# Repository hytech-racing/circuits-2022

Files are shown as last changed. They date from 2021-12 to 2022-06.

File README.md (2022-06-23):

HyTech Logo

# 2022 Circuits

Repository for all of the circuits for the 2021-2022 car.

## Getting Started with this Git Repository
1. Create a GitHub account if you don't already have one.
2. Follow HyTech's [Software Guide](https://github.com/hytech-racing/training/tree/master/Resources).
3. Download and install [GitHub Desktop](https://desktop.github.com/) (basic) or [Git CLI](https://git-scm.com/book/en/v2/Getting-Started-Installing-Git) (advanced).
    * If you are using GitHub Desktop for the first time, be sure to read the [User Guide](https://help.github.com/desktop/guides/).
    * If you are using Git for the first time, you should start off by reading a tutorial. There are many available online:
        * [Git Tutorial](https://git-scm.com/docs/gittutorial)
        * [Atlassian Git Tutorial](https://www.atlassian.com/git/tutorials/)
    * You may want to keep a copy of [GitHub's Git Cheat Sheet](https://services.github.com/kit/downloads/github-git-cheat-sheet.pdf) as a reference.
4. Talk to your subteam lead to be added to the team within the GitHub organization.
5. Clone this repository to your computer using the URLs:
    * SSH: `git@github.com:hytech-racing/circuits-2022.git`
    * HTTPS: `https://github.com/hytech-racing/circuits-2022.git`

## Getting Started with EAGLE
1. Follow HyTech's [Software Guide](https://github.com/hytech-racing/training/tree/master/Resources).
2. Download and install Autodesk [EAGLE](https://www.autodesk.com/products/eagle/overview)
3. Get the free [Educational License](https://www.autodesk.com/education/free-software/eagle) (a .edu email address is required)

## Github Software Guidelines and Electrical Designs Rules Review Process
Follow HyTech's [Github Software Guidelines](https://gtvault.sharepoint.com/:w:/r/sites/HyTechRacing2/Shared%20Documents/Electrical%20-%20All/HT06/Guidelines%20Rules%20and%20Procedures/Github%20Software%20Guide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) to understand our development flow and pull request procedure.
Follow HyTech's [Electrical Designs Rules Review Process](https://gtvault.sharepoint.com/:w:/r/sites/HyTechRacing2/Shared%20Documents/Electrical%20-%20All/HT06/Guidelines%20Rules%20and%20Procedures/Electrical%20Designs%20Ru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) to understand circuit design flow. 

## Circuit Board Versioning Scheme
* New boards must start their numbering at revision 1.
* Revision numbers must be incremented by 1 when a physical board is manufactured, but not at any other time.
* After a board is manufactured, the files corresponding to the manufactured version should not be modified.
* Circuit boards based off of a previous year's design should increment based off of the previous board's revision number.

## More Information
* [Software Guide](https://github.com/hytech-racing/training/tree/master/Resources)
* [Team Site](https://hytechracing.gatech.edu/)
* [Facebook](https://www.facebook.com/HyTechRacing/)
* [Instagram](https://www.instagram.com/hytech.racing/)
* [Engage](https://gatech.campuslabs.com/engage/organization/hytech-racing)

## License
This project is licensed under the GPL License v3.0. See the [LICENSE](LICENSE) file for more information.

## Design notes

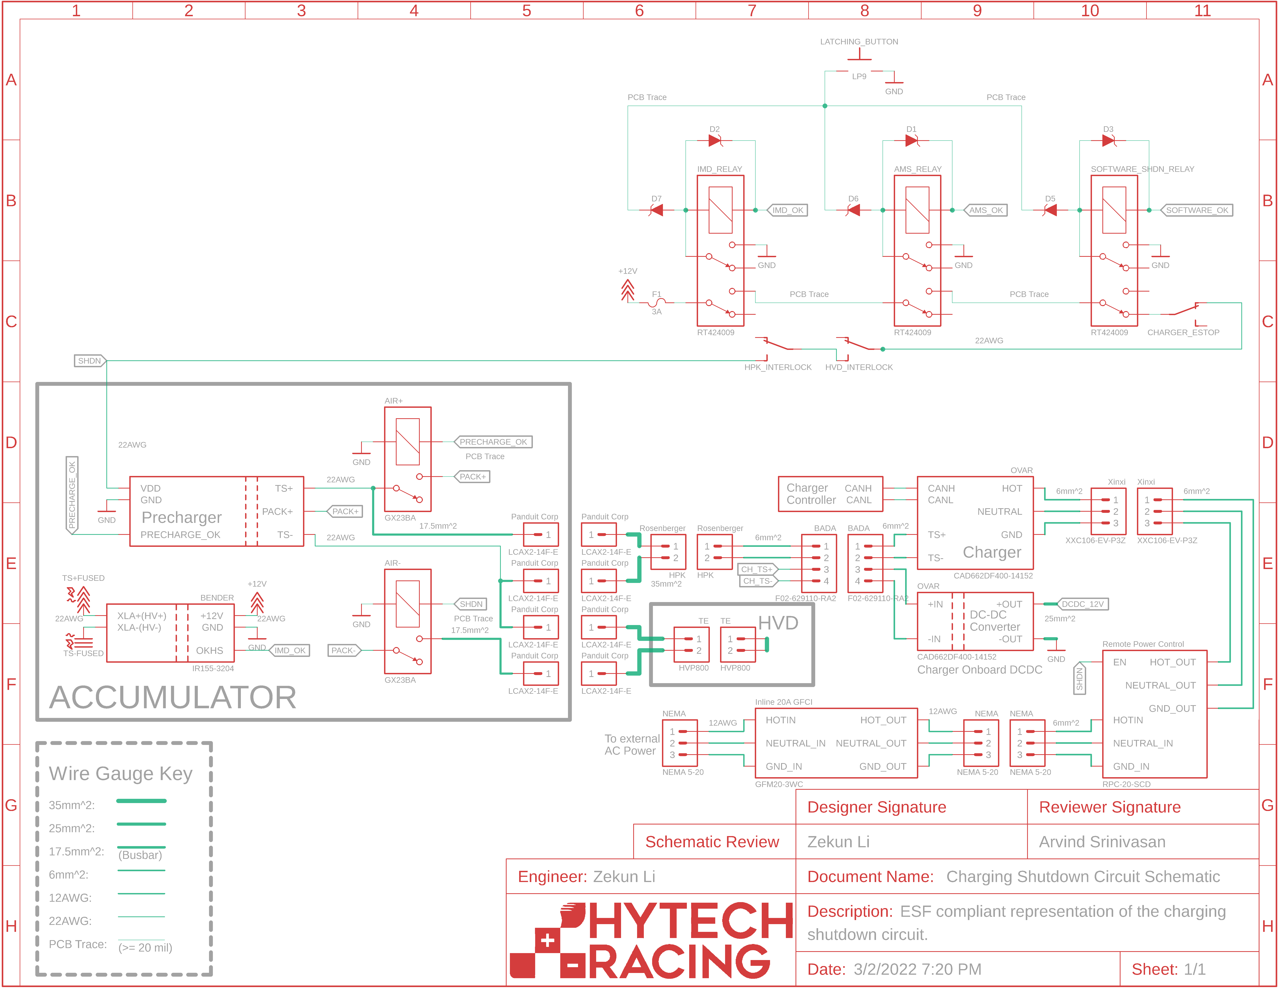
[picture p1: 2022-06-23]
ESF Schematics/2022/Charging Shutdown Circuit Schematic.png

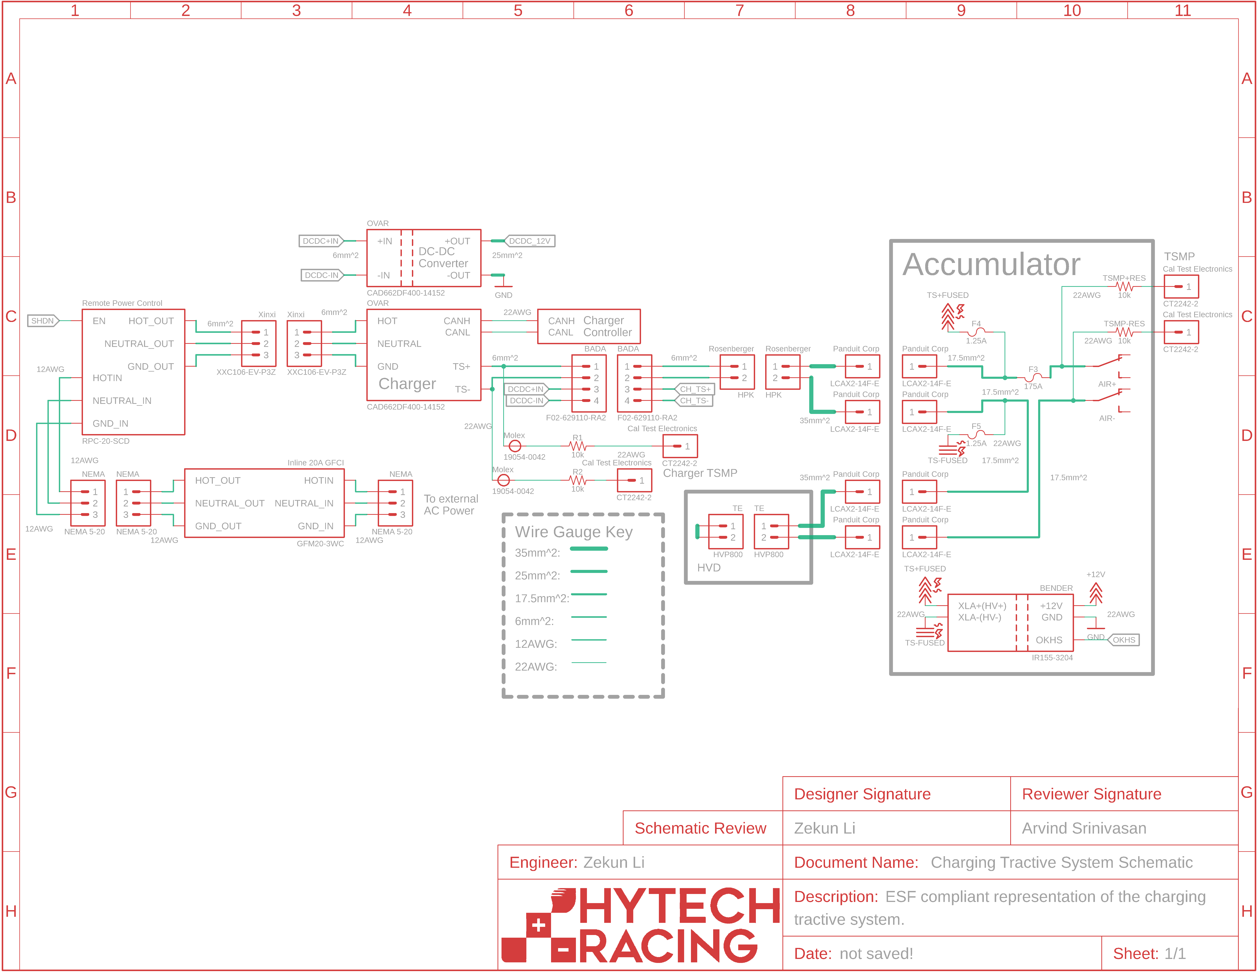
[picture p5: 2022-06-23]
ESF Schematics/2022/Charging Tractive System Schematic.png

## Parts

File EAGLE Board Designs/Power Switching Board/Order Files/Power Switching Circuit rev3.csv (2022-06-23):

Board Quantity | Ordering Quantity | Value | Reference | ATTRITION | CAPACITANCE | COLOR | CURRENT | DKPN | ESR | FUSE_TYPE | MANUFACTURER | MOPN | MPN | POWER | RESISTANCE | TOLERANCE | VOLTAGE | VOLTAGE_CONTINUOUS | VOLTAGE_MAX
1 | 11 | CAPACITOR_0603_10V_1UF | C11 | 1000 | 1µF |  |  | 311-1796-1-ND |  |  | Yageo | 603-CC603KRX7R6BB105 | CC0603KRX7R6BB105 |  |  | 10% | 10V
1 | 11 | CAPACITOR_0603_10V_680PF | C9 | 1000 | 680pF |  |  | 732-7757-1-ND |  |  | Würth Elektronik | 710-885012006013 | 885012006013 |  |  | 5% | 10V
2 | 12 | CAPACITOR_0603_10V_68NF | C8, C13 | 500 | 68nF |  |  | 399-C0603C683K8RAC7867CT-ND |  |  | KEMET | 80-C0603C683K8R | C0603C683K8RACTU |  |  | 10% | 10V
3 | 13 | CAPACITOR_0603_25V_0.1UF | C10, C100, C103 | 333 | 0.1µF |  |  | 1276-1006-1-ND |  |  | Samsung Electro-Mechanics | 187-CL10B104KA8NNNC | CL10B104KA8NNNC |  |  | 10% | 25V
4 | 14 | CAPACITOR_0603_25V_10UF | C2, C4, C7, C102 | 250 | 10µF |  |  | 490-7202-1-ND |  |  | Murata Electronics | 81-GRM188R61E106MA3D | GRM188R61E106MA73D |  |  | 20% | 25V
3 | 13 | CAPACITOR_0603_25V_1UF | C3, C101, C104 | 333 | 1µF |  |  | 1276-1184-1-ND |  |  | Samsung Electro-Mechanics | 187-CL10B105KA8NNNC | CL10B105KA8NNNC |  |  | 10% | 25V
2 | 12 | CAPACITOR_0603_25V_47NF | C5, C6 | 500 | 47nF |  |  | 478-6340-1-ND |  |  | Kyocera AVX | 581-06033C473K42ZA | 06033C473K4Z2A |  |  | 10% | 25V
1 | 11 | CAPACITOR_0603_35V_1UF | C12 | 1000 | 1µF |  |  | 445-173625-1-ND |  |  | TDK Corporation | 810-C1608X7R1V105KAE | C1608X7R1V105K080AE |  |  | 10% | 35V
1 | 11 | CAPACITOR_1206_25V_33UF | C105 | 1000 | 33µF |  |  | 445-8046-1-ND |  |  | TDK Corporation | 810-C3216X5R1E336M | C3216X5R1E336M160AC |  |  | 20% | 25V
1 | 3 | CONNECTOR-3_8STA20435PN | J2 | 200 |  |  |  |  |  |  | Souriau |  | 8STA20435PN
2 | 4 | CONNECTOR-4_SOURIAU_ | J1, J3 | 100 |  |  |  |  |  |  | Souriau |  | 8STA21204PN
1 | 3 | EEUFP1E681 | C1 | 200 | 680uF |  |  | P123947-ND | 0.068 |  | Panasonic Electronic Components | 667-EEU-FP1E681 | EEU-FP1E681 |  |  | 20% | 25V
4 | 6 | FUSE_HOLDER_MINIBLADEPTH | XF1, XF2, XF3, XF4 | 50 |  |  |  | 36-3568-ND |  | MINI 297 | Keystone | 534-3568 | 3568
4 | 8 | FUSE_MINI_BLADE_10 | O1, O2, O3, O4 | 100 |  |  |  | F991-ND |  |  | Littelfuse Inc. | 576-0297010.WXNV | 0297010.WXNV
4 | 14 | LED_0603_BLUE | D7, D8, D9, D17 | 250 |  | Blue |  | 754-1789-1-ND |  |  | Kingbright | 604-APT1608VBC/D | APT1608VBC/D
2 | 12 | LED_0603_GREEN | D11, D12 | 500 |  | Green |  | 754-1790-1-ND |  |  | Kingbright | 604-APT1608ZGCK | APT1608ZGCK
1 | 11 | LED_0603_ORANGE | D10 | 1000 |  | Orange |  | 754-1120-1-ND |  |  | Kingbright | 604-APT1608SECK | APT1608SECK
2 | 12 | LED_0603_RED | D15, D16 | 500 |  | Red |  | 754-1786-1-ND |  |  | Kingbright | 604-APT1608SECKJ3PRV | APT1608SECK/J3-PRV
2 | 12 | LED_0603_YELLOW | D13, D14 | 500 |  | Yellow |  | 754-1788-1-ND |  |  | Kingbright | 604-APT1608SYCK/J3-PRV | APT1608SYCK/J3-PRV
1 | 3 | LTC4421 | U1 | 200 |  |  |  | 161-LTC4421CG#PBF-ND |  |  | Analog Devices Inc. | 584-LTC4421CG#PBF | LTC4421CG#PBF
1 | 3 | RELAY_SOLIDSTATE_NO_CMX60D20 | K1 | 200 |  |  |  | CC1666-ND |  |  | Crydom | 558-CMX60D20 | CMX60D20
2 | 12 | RESISTOR_0603_1.13M | R11, R26 | 500 |  |  |  | 541-1.13MHCT-ND |  |  | Vishay Dale | 71-CRCW06031M13FKEA | CRCW06031M13FKEA | 0.1W | 1.13M | 1% |  | 75V | 100V
4 | 14 | RESISTOR_0603_10K | R1, R2, R3, R22 | 250 |  |  |  | 311-10.0KHRCT-ND |  |  | Yageo | 603-RC0603FR-0710KL | RC0603FR-0710KL | 0.1W | 10k | 1% |  | 31.62V | 75V
2 | 12 | RESISTOR_0603_13K | R9, R24 | 500 |  |  |  | P13KBECT-ND |  |  | Panasonic Electronic Components | 667-ERA-3ARW133V | ERA-3ARW133V | 0.1W | 13k | 0.05% |  | 75V | 150V
10 | 20 | RESISTOR_0603_1K | R12, R13, R14, R15, R16, R17, R18, R19, R20, R21 | 100 |  |  |  | 311-1.00KHRCT-ND |  |  | Yageo | 603-RC0603FR-071KL | RC0603FR-071KL | 0.1W | 1k | 1% |  | 10.00V | 75V
2 | 12 | RESISTOR_0603_41.2K | R7, R23 | 500 |  |  |  | P20155CT-ND |  |  | Panasonic Electronic Components | 667-ERJ-PB3B4122V | ERJ-PB3B4122V | 0.2W | 41.2k | 0.1% |  | 150V | 200V
2 | 12 | RESISTOR_0603_5.49K | R10, R25 | 500 |  |  |  | P20367CT-ND |  |  | Panasonic Electronic Components | 667-ERJ-PB3D5491V | ERJ-PB3D5491V | 0.2W | 5.49k | 0.5% |  | 150V | 200V
2 | 12 | RESISTOR_0603_DNP | R100, R101 | 500 |  |  |  |  |  |  |  |  |  |  | DNP
2 | 12 | RESISTOR_0805_0.62 | R6, R8 | 500 |  |  |  | 311-.62SCT-ND |  |  | Yageo | 603-RL0805FR-070R62L | RL0805FR-070R62L | 0.125W | 0.62 | 1% |  | 0.28V | 0.70V
2 | 4 | RESISTOR_SENSE__WSL40262L000FEB | R4, R5 | 100 |  |  |  | WSLR-.002CT-ND |  |  | Vishay Dale | 71-WSL40262L000FEB | WSL40262L000FEB | 3W | 2.0mΩ | 1% | 0.077V
2 | 4 | SCHOTTKY_SOD323_30V | D2, D3 | 100 |  |  | 0.8A | CUS08F30H3FTR-ND |  |  | Toshiba Semiconductor and Storage | 757-CUS08F30H3F | CUS08F30 |  |  |  | 30V
12 | 14 | TEST_POINT | TP1, TP2, TP3, TP4, TP5, TP6, TP7, TP8, TP9, TP10, TP11, TP12 | 17 |  |  |  | 36-5015CT-ND |  |  | Keystone Electronics | 534-5015 | 5015
4 | 6 | TRANSISTOR_N_MOS_2-7K1S_TK100S04N1LLQ | Q1, Q2, Q3, Q4 | 50 |  |  |  | TK100S04N1LLQCT-ND |  |  | Toshiba Semiconductor and Storage | 757-TK100S04N1LLQ | TK100S04N1L | LQ
4 | 6 | TVS_15V | D1, D4, D5, D6 | 50 |  |  |  | GSOT15-E3-08CT-ND |  |  | Vishay General Semiconductor - Diodes Division | 78-GSOT15-E3-08 | GSOT15-E3-08 |  |  |  | 15V
1 | 3 | UWE-12/10-Q12PB-C | A1 | 200 |  |  |  | 811-3061-ND |  |  | Murata Power Solutions Inc. | 580-UWE-12/10Q12PBC | UWE-12/10-Q12PB-C

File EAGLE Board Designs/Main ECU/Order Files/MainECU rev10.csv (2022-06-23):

Board Quantity | Ordering Quantity | Value | Reference | ATTRITION | __EXTERNAL__
5 |  |  | C40, C41, CAL_BRAKE, R44, R45
41 |  | 0.1uF | C1, C3, C5, C6, C7, C8, C11, C12, C13, C14, C15, C16, C17, C18, C19, C21, C22, C24, C25, C26, C27, C28, C29, C31, C36, C37, C39, C42, C44, C47, C48, C49, C50, C102, C106, C111, C113, C115, C117, C119, C121
1 |  | 0.47uF | C9
2 |  | 10.2k | R40, R109
1 |  | 100 | R43
1 |  | 100k | R39
24 |  | 10k | BR1, BR2, PD1, PD2, PU1, PU2, R1, R31, R36, R37, R42, R46, R103, R104, R113, R116, R117, R120, R123, R125, R126, R127, R128, R130
4 |  | 10uF | C104, C105, C108, C109
2 |  | 1130 | R41, R108
4 |  | 12V_TEST | 12V_TEST, ACCEL1_BUFF_TEST, READ_ACCEL1_TEST, SIGNAL_ACCEL1_TEST
10 |  | 12k | R111, R119, R131, R132, R133, R134, R135, R136, R137, R138
2 |  | 147 | R3, R16
1 |  | 14k | R38
4 |  | 150 | R105, R106, R107, R112
1 |  | 15nF | C30
3 |  | 1k | R8, R9, R10
11 |  | 1uF | C2, C4, C20, C35, C101, C107, C112, C114, C116, C118, C120
1 |  | 2.2uF | C32
1 |  | 200 | R5
3 |  | 215 | R15, R19, R35
4 |  | 2k | R121, R124, R129, R139
1 |  | 3.3V | REG1
2 |  | 30 | R2, R4
2 |  | 30.1 | R17, R18
1 |  | 324 | R34
1 |  | 330 | R32
1 |  | 4.02k | R118
1 |  | 4.7lk | R114
1 |  | 4.7nF | C100
10 |  | 43k | R20, R21, R22, R23, R24, R25, R26, R27, R102, R110
7 |  | 470pF | C10, C23, C33, C38, C43, C45, C46
1 |  | 470uF | C103
2 |  | 47nF | C34, C110
1 |  | 5.1k | R115
3 |  | 5A | 5ABOARDFUSE1, 5AFUSE1, 5ASHUTDOWNFUSE1
1 |  | 5V | REG2
2 |  | 60.4 | R100, R101
4 |  | 68 | R28, R29, R30, R122
1 |  | 680k | R33
1 |  | 866 | R11
2 |  | 909 | R6, R7
3 |  | 976 | R12, R13, R14
2 |  | ACHS-7121 | U35, U103
4 |  | Blue | 3V3, 5V, A, MQTT_CONN
1 |  | CDSOT23-T24CAN-Q | U36
1 |  | CONNECTOR-37 | X100
1 |  | CONNECTOR-4AUTOSPORT | X101
2 |  | CONNECTOR-4NANO-FIT-VERTICAL-4 | X1, X2
1 |  | CR-2450/G1AN | U109
2 |  | DMG3406L | Q101, Q102
1 |  | G5LE | INVERTER_PWR_RELAY1
4 |  | Green | B, OKHS, RSSI, WDGT
1 |  | JUMPER.1 | J1
2 |  | LM293DG4 | U10, U23
1 |  | M02_SLIM | CAN_TERM_JMP1
7 |  | MAX7480 | U7, U24, U33, U38, U39, U44, U45
1 | 3 | MC34152 | U102 | 200
2 |  | MCP2551 | CAN100, CAN101
2 |  | MCP3204 | U8, U37
4 |  | MCP6002SOIC | U100, U101, U104, U105
9 |  | MMBZ5246BLT1G | D9, D10, D11, D12, D100, D101, D102, D104, D108
1 |  | MTK3339 | MTK3339_BREAKOUT
2 |  | N-CHANNEL_MOSFET_IRF1324PBF | U41, U42
6 |  | OPA990IDBVR | U6, U17, U19, U28, U29, U106
2 |  | Orange | BSPD, D
3 |  | P-CHANNEL_MOSFET_DMP3099L-7 | Q1, Q100, Q103
4 |  | RT424009 | IMD_SHUTDOWN_RLY1, U2, U3, U4
6 |  | Red | ASSOC, BRAKE, CUOK, E, INV, SWOK
2 |  | SN74AHC1G09 | U11, U107
2 |  | SN74LVC1G32 | U18, U25
1 |  | STWD100PYW83F | U108
1 |  | Switch | S1
1 |  | TEENSY_3.2_SIMPLE | U5
1 |  | TEENSY_3.5_EXT | U1
27 |  | TEST_POINTMICRO_MINIATURE | 3V3_TEST, ACCEL2_BUFF_TEST, BRAKE1_BUFF_TEST, BRAKE2_BUFF_TEST, READ_ACCEL2_TEST, READ_BRAKE1_TEST, READ_BRAKE2_TEST, SIGNAL_ACCEL2_TEST, SIGNAL_BRAKE1_TEST, SIGNAL_BRAKE2_TEST, SIGNAL_GND, U12, U13, U14, U15, U16, U20, U21, U22, U26, U27, U30, U31, U32, U40, U43, U46
1 |  | THERMISTOR_NCP210805 | BOARD_TEMP
17 |  | TS4148 RYG | D1, D2, D3, D4, D5, D6, D7, D8, D103, D105, D106, D107, D109, D110, D111, D112, D113
2 |  | TXB0104TSSOP | U9, U34
1 |  | White | LATCH
1 |  | XBEE | XBEE
3 |  | Yellow | BMS, C, CURRENT

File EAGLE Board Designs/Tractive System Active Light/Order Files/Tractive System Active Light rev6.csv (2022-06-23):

Board Quantity | Ordering Quantity | Value | Reference | ATTRITION | COLOR | DKPN | GAUGE | MANUFACTURER | MOPN | MPN | POWER | RESISTANCE | TOLERANCE | VOLTAGE_CONTINUOUS | VOLTAGE_MAX
1 | 3 | CONNECTOR-4_μF_S_RA_ | J1 | 200 |  | WM1832CT-ND |  | Molex | 538-0430450411 | 0430450411
4 | 8 | CRIMP_MICROFIT_20-24 | O2, O3, O4, O5 | 100 |  | WM2776CT-ND | 20-24 | Molex | 538-43030-0003 | 0430300003
4 | 6 | LED_RGB_ASMG-PT00-00001 | D1, D2, D3, D4 | 50 | RGB | 516-4178-2-ND |  | Broadcom Limited | 630-ASMG-PT00-00001 | ASMG-PT00-00001
1 | 2 | RECEPTACLE-4_MICROFIT | O1 | 100 |  | WM11225-ND |  | Molex | 538-43025-0408 | 0430250408
1 | 11 | RESISTOR_0805_36 | R1 | 1000 |  | P36ADTR-ND |  | Panasonic Electronic Components | 667-ERJ-P06J360V | ERJ-P06J360V | 0.5W | 36 | 5% | 4.243V | 400V
1 | 11 | RESISTOR_0805_5.1 | R3 | 1000 |  | P19237TR-ND |  | Panasonic Electronic Components | 667-ERJ-6DQJ5R1V | ERJ-6DQJ5R1V | 0.5W | 5.1 | 5% | 1.597V | 400V

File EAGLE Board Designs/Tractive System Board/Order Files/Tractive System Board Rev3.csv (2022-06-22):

Board Quantity | Ordering Quantity | Value | Reference | ATTRITION | CAPACITANCE | COLOR | CURRENT | CURRENT_RATED | CURRENT_SATURATION | DCR | DKPN | GAUGE | INDUCTANCE | MANUFACTURER | MOPN | MPN | POWER | RESISTANCE | TOLERANCE | VOLTAGE | VOLTAGE_CONTINUOUS | VOLTAGE_MAX
5 | 15 | CAPACITOR_0603_10V_0.1UF | C23, C102, C105, C106, C108 | 200 | 0.1µF |  |  |  |  |  | 720-1688-1-ND |  |  | Vishay Vitramon | 77-VJ0603Y104JXQPBC | VJ0603Y104JXQPW1BC |  |  | 5% | 10V
3 | 13 | CAPACITOR_0603_10V_10NF | C7, C15, C16 | 333 | 10nF |  |  |  |  |  | 311-4054-1-ND |  |  | Yageo | 603-CC603KRX7R6BB103 | CC0603KRX7R6BB103 |  |  | 10% | 10V
8 | 18 | CAPACITOR_0603_10V_1UF | C17, C18, C19, C20, C21, C22, C103, C107 | 125 | 1µF |  |  |  |  |  | 311-1796-1-ND |  |  | Yageo | 603-CC603KRX7R6BB105 | CC0603KRX7R6BB105 |  |  | 10% | 10V
1 | 11 | CAPACITOR_0603_10V_4.7UF | C101 | 1000 | 4.7µF |  |  |  |  |  | 1276-1044-1-ND |  |  | Samsung Electro-Mechanics | 187-CL10A475KP8NNNC | CL10A475KP8NNNC |  |  | 10% | 10V
2 | 12 | CAPACITOR_0603_25V_0.1UF | C14, C100 | 500 | 0.1µF |  |  |  |  |  | 1276-1006-1-ND |  |  | Samsung Electro-Mechanics | 187-CL10B104KA8NNNC | CL10B104KA8NNNC |  |  | 10% | 25V
1 | 11 | CAPACITOR_0603_25V_10UF | C110 | 1000 | 10µF |  |  |  |  |  | 490-7202-1-ND |  |  | Murata Electronics | 81-GRM188R61E106MA3D | GRM188R61E106MA73D |  |  | 20% | 25V
3 | 13 | CAPACITOR_0603_25V_1UF | C13, C104, C111 | 333 | 1µF |  |  |  |  |  | 1276-1184-1-ND |  |  | Samsung Electro-Mechanics | 187-CL10B105KA8NNNC | CL10B105KA8NNNC |  |  | 10% | 25V
1 | 11 | CAPACITOR_0603_35V_0.1UF | C112 | 1000 | 0.1µF |  |  |  |  |  | 587-3354-1-ND |  |  | Taiyo Yuden | 963-GMK107B7104KAHT | GMK107B7104KAHT |  |  | 10% | 35V
1 | 11 | CAPACITOR_0805_25V_22UF | C12 | 1000 | 22µF |  |  |  |  |  | 311-1903-1-ND |  |  | Yageo | 603-CC805MKX5R8BB226 | CC0805MKX5R8BB226 |  |  | 20% | 25V
2 | 12 | CAPACITOR_1206_250V_0.1UF | C4, C11 | 500 | 0.1uF |  |  |  |  |  | 445-6079-2-ND |  |  | TDK Corporation | 810-C3216X7R2E104KT5 | C3216X7R2E104K160AM |  |  | 10% | 250V
3 | 5 | CAPACITOR_2220_250V_1UF | C5, C8, C109 | 67 | 1µF |  |  |  |  |  | 445-2304-2-ND |  |  | TDK Corporation | 810-C5750X7R2E105K | C5750X7R2E105K230KA |  |  | 10% | 250V
2 | 4 | CAPACITOR_2220_630V_0.1UF | C2, C10 | 100 | 0.1uF |  |  |  |  |  | 445-11980-2-ND |  |  | TDK Coporation | 810-C5750CH2J104K2KC | C5750CH2J104K280KC |  |  | 10% | 630V
3 | 5 | CAPACITOR_2220_630V_1UF | C3, C6, C9 | 67 | 1µF |  |  |  |  |  | 1608-2220Y6300105KXTWS2CT-ND |  |  | Knowles Syfer | 843-2220Y63105KXTWS2 | 2220Y6300105KXTWS2 |  |  | 10% | 630V
1 | 3 | CAPACITOR_POLAR__3600UF | C1 | 200 | 3600uF |  |  |  |  |  | 565-EKYC250ELL362ML20S-ND |  |  | United Chemi-con | 661-YC250ELL362ML20S | EKYC250ELL362ML20S |  |  |  | 25V
1 | 3 | CONNECTOR-4__ | J1 | 200 |  |  |  |  |  |  |  |  |  | Molex |  | 2068320423
1 | 3 | CONNECTOR-5_MICRO_V6S_ | J2 | 200 |  |  |  |  |  |  |  |  |  | Molex |  | 2165713006
1 | 3 | CONNECTOR-5_MICRO_V7S_ | J3 | 200 |  |  |  |  |  |  |  |  |  | Molex |  | 2165713007
1 | 3 | CONNECTOR-8_S_S | J4 | 200 |  |  |  |  |  |  | S7107-ND |  |  | Sullins Connector Solutions |  | PPPC042LFBN-RC
14 | 28 | CRIMP_MICROFIT_20-24 | O9, O10, O11, O12, O13, O14, O15, O16, O17, O18, O19, O20, O21, O22 | 100 |  |  |  |  |  |  | WM2776CT-ND | 20-24 |  | Molex | 538-43030-0003 | 0430300003
1 | 3 | DCM4623TD2J13D0T70 | U103 | 200 |  |  |  |  |  |  | 1102-DCM4623TD2J13D0T70-ND |  |  | Vicor | 492-DCM4623D2J13D0T7 | DCM4623TD2J13D0T70
2 | 4 | FUSE_0885_1.25 | F1, F2 | 100 |  |  | 1.25A |  |  |  | F10986CT-ND |  |  | Littelfuse Inc. | 576-08851.25DR | 08851.25DR |  |  |  | 500V
1 | 3 | FUSE_HOLDER_MINIBLADEPTH | XF1 | 200 |  |  |  |  |  |  | 36-3568-ND |  |  | Keystone | 534-3568 | 3568
1 | 2 | FUSE_MINI_BLADE_10 | O25 | 100 |  |  |  |  |  |  | F991-ND |  |  | Littelfuse | 576-0297010.WXNV | 0297010.WXNV
1 | 3 | INDUCTOR_PA4334_3.6UH | L1 | 200 |  |  |  | 1.6A | 1A | 0.13Ω | 553-3508-2-ND |  | 3.6µH | Pulse Electonics Company | 673-PA4334362NLT | PA4334.362NLT
1 | 3 | INDUCTOR_SRU1048_330UH | L3 | 200 |  |  |  | 0.65A | 0.52A | 0.640Ω | SRU1048-331YTR-ND |  | 330µH | Bourns Inc. | 652-SRU1048-331Y | SRU1048-331Y |  |  | 30%
1 | 3 | INDUCTOR_WELMHI_56UH | L2 | 200 |  |  |  | 1.4A | 2A | 342mΩ | 732-11454-2-ND |  | 56µH | Wurth Elektronik | 710-74437349560 | 74437349560 |  |  | 20%
2 | 4 | ISO224B_AIRGAP | U2, U3 | 100 |  |  |  |  |  |  | 296-52316-1-ND |  |  | Texas Instruments | 595-ISO224BDWVR | ISO224BDWVR
4 | 14 | LED_0603_BLUE | D1, D4, D6, D9 | 250 |  | Blue |  |  |  |  | 754-1789-1-ND |  |  | Kingbright | 604-APT1608VBC/D | APT1608VBC/D
1 | 11 | LED_0603_GREEN | D10 | 1000 |  | Green |  |  |  |  | 754-1790-1-ND |  |  | Kingbright | 604-APT1608ZGCK | APT1608ZGCK
1 | 11 | LED_0603_ORANGE | D11 | 1000 |  | Orange |  |  |  |  | 754-1120-1-ND |  |  | Kingbright | 604-APT1608SECK | APT1608SECK
1 | 11 | LED_0603_RED | D2 | 1000 |  | Red |  |  |  |  | 754-1786-1-ND |  |  | Kingbright | 604-APT1608SECKJ3PRV | APT1608SECK/J3-PRV
1 | 11 | LED_0603_WHITE | D7 | 1000 |  | White |  |  |  |  | SM0603UWC-ND |  |  | Bivar Inc. | 749-SM0603UWC | SM0603UWC
1 | 11 | LED_0603_YELLOW | D8 | 1000 |  | Yellow |  |  |  |  | 754-1788-1-ND |  |  | Kingbright | 604-APT1608SYCK/J3-PRV | APT1608SYCK/J3-PRV
1 | 3 | LTC3639 | U1 | 200 |  |  |  |  |  |  | LTC3639EMSE#TRPBFTR-ND |  |  | Analog Devices Inc. | 584-LTC3639EMSETRPBF | LTC3639EMSE#TRPBF
2 | 4 | LTC6994-2 | U100, U101 | 100
1 | 2 | RECEPTACLE-4_MICROFIT | O23 | 100 |  |  |  |  |  |  | WM11225-ND |  |  | Molex | 538-43025-0408 | 0430250408
1 | 2 | RECEPTACLE-6_SINGLE_MICROFIT | O3 | 100 |  |  |  |  |  |  | WM13217-ND |  |  | Molex | 538-43645-0608 | 0436450608
1 | 2 | RECEPTACLE-7_MICROFIT | O2 | 100 |  |  |  |  |  |  | WM2405-ND |  |  | Molex | 538-43645-0700 | 0436450700
1 | 2 | RECEPTACLE-8_FLEXSTACK | O1 | 100 |  |  |  |  |  |  | ZW-04-11-G-D-522-158-ND |  |  | Samtec Inc | 200-ZW0411GD522158 | ZW-04-11-G-D-522-158
1 | 3 | RECTIFIER_400V_SOD123 | D102 | 200 |  |  | 1A |  |  |  | US1GWF-7DITR-ND |  |  | Diodes Incorporated | 621-US1GWF-7 | US1GWF-7 |  |  |  | 400V
1 | 3 | RELAY_SOLIDSTATE_NC_AG | K100 | 200 |  |  |  |  |  |  | 255-2897-ND |  |  | Panasonic Industrial Devices | 769-AQY414EHA | AQY414EHA
1 | 3 | RELAY_SOLIDSTATE_NO_AG | K3 | 200 |  |  |  |  |  |  | 255-1436-5-ND |  |  | Panasonic Inustrial Devices | 769-AQY214EHA | AQY214EHA
1 | 3 | RELAY_SPST_NC_POLARIZED_3550_12 | K2 | 200 |  |  |  |  |  |  | 1835-1040-ND |  |  | Comus International |  | 3350-4275-126
1 | 3 | RELAY_SPST_NO_3550_12 | K1 | 200 |  |  |  |  |  |  | 1835-1037-ND |  |  | Comus International |  | 3350-1275-126
1 | 11 | RESISTOR_0603_1.62 | R3 | 1000 |  |  |  |  |  |  | 1712-CPF0603B1R62E1TR-ND |  |  | TE Conductivity Passive Product | 279-CPF0603B1R62E1 | CPF0603B1R62E1 | 0.1W | 1.62 | 0.1% |  | 0.51V | 50V
1 | 11 | RESISTOR_0603_10 | R24 | 1000 |  |  |  |  |  |  | 311-10.0HRCT-ND |  |  | Yageo | 603-RC0603FR-0710RL | RC0603FR-0710RL | 0.1W | 10 | 1% |  | 1.00V | 75V
2 | 12 | RESISTOR_0603_10K | R5, R23 | 500 |  |  |  |  |  |  | 311-10.0KHRCT-ND |  |  | Yageo | 603-RC0603FR-0710KL | RC0603FR-0710KL | 0.1W | 10k | 1% |  | 31.62V | 75V
1 | 11 | RESISTOR_0603_13.3K | R109 | 1000 |  |  |  |  |  |  | P20099TR-ND |  |  | Panasonic Electronic Components | 667-ERJ-PB3B1332V | ERJ-PB3B1332V | 0.2W | 13.3k | 0.1% |  |  | 75k
1 | 11 | RESISTOR_0603_180 | R9 | 1000 |  |  |  |  |  |  | 311-180HRCT-ND |  |  | Yageo | 603-RC0603FR-07180RL | RC0603FR-07180RL | 0.1W | 180 | 1% |  | 4.24V | 75V
11 | 21 | RESISTOR_0603_1K | R1, R4, R6, R25, R26, R27, R28, R29, R30, R31, R106 | 91 |  |  |  |  |  |  | 311-1.00KHRCT-ND |  |  | Yageo | 603-RC0603FR-071KL | RC0603FR-071KL | 0.1W | 1k | 1% |  | 10.00V | 75V
1 | 11 | RESISTOR_0603_3.32K | R113 | 1000 |  |  |  |  |  |  | YAG1651TR-ND |  |  | Yageo | 603-RT0603BRD073K32L | RT0603BRD073K32L | 0.1W | 3.32k | 0.1% |  | 18.22V | 75V
2 | 12 | RESISTOR_0603_33.2K | R20, R21 | 500 |  |  |  |  |  |  | P20144TR-ND |  |  | Panasonic Electronic Components | 667-ERJ-PB3B3322V | ERJ-PB3B3322V | 0.1W | 33.2k | 0.1% |  | 57.61V | 75V
2 | 12 | RESISTOR_0603_360K | R14, R15 | 500 |  |  |  |  |  |  | RHM360KAYTR-ND |  |  | Rohm Semiconductor | 755-KTR03EZPF3603 | KTR03EZPF3603 | 0.1W | 360k | 1% |  | 189.74V | 350V
2 | 12 | RESISTOR_0603_39 | R2, R22 | 500 |  |  |  |  |  |  | 13-RT0603BRD0739RLTR-ND |  |  | Yageo | 603-RT0603BRD0739RL | RT0603BRD0739RL | 0.1W | 39 | 1% |  |  | 75V
3 | 13 | RESISTOR_0603_75K | R101, R104, R107 | 333 |  |  |  |  |  |  | RT0603BRE0775KL-ND |  |  | Yageo | 603-RT0603BRE0775KL | RT0603BRE0775KL | 0.1W | 75k | 0.1% |  | 75V | 75V
1 | 11 | RESISTOR_0603_8.35K | R108 | 1000 |  |  |  |  |  |  | 764-1461-2-ND |  |  | Vishay Dale Thin Film | 71-PTN0603E8351BST1 | PTN0603E8351BST1 | 0.15W | 8.35k | 0.1% |  | 28.90V | 75V
1 | 11 | RESISTOR_0603_DNP | R111 | 1000 |  |  |  |  |  |  |  |  |  |  |  |  |  | DNP
2 | 12 | RESISTOR_0603_HV750K | R11, R12 | 500 |  |  |  |  |  |  | RHM75KAYTR-ND |  |  | Rohm | 755-KTR03EZPF7502 | KTR03EZPF7502 | 0.1W | 750k | 1% |  |  | 350V
4 | 14 | RESISTOR_0603_HV75K | R16, R17, R18, R19 | 250 |  |  |  |  |  |  | RHM750KAYTR-ND |  |  | Rohm | 755-KTR03EZPF7503 | KTR03EZPF7503 | 0.1W | 75k | 1% |  |  | 350V
2 | 12 | RESISTOR_0805_1M | R100, R103 | 500 |  |  |  |  |  |  | P20936TR-ND |  |  | Panasonic Electronic Components | 667-ERJ-PB6B1004V | ERJ-PB6B1004V | 0.25W | 1M | 0.1% |  | 150V | 150V
2 | 12 | RESISTOR_0805_523K | R102, R105 | 500 |  |  |  |  |  |  | P20904TR-ND |  |  | Panasonic Electronic Components | 667-ERJ-PB6B5233V | ERJ-PB6B5233V | 0.25W | 523k | 0.1% |  | 150V | 150V
1 | 11 | RESISTOR_0805_976K | R110 | 1000 |  |  |  |  |  |  | P20935TR-ND |  |  | Panasonic Electronic Components | 667-ERJ-PB6B9763V | ERJ-PB6B9763V | 0.25W | 976k | 0.1% |  | 150V | 150V
1 | 11 | RESISTOR_0805_HV365K | R112 | 1000 |  |  |  |  |  |  | RHM365KAHTR-ND |  |  | Rohm | 755-KTR10EZPF3653 | KTR10EZPF3653 | 0.125W | 365k | 1% |  | 213V | 350V
3 | 5 | RESISTOR_B20_10K | R7, R8, R13 | 67 |  |  |  |  |  |  | B20J10KE-ND |  |  | Ohmite | 588-B20J10KE | B20J10KE | 20W | 10k | 5% |  | 447V | 750V
1 | 3 | RESISTOR_B20_750 | R10 | 200 |  |  |  |  |  |  | B20J750E-ND |  |  | Ohmite | 588-B20J750E | B20J750E | 20W | 750 | 5% |  | 122V | 750V
3 | 5 | SCHOTTKY_SOD323_30V | D3, D100, D101 | 67 |  |  | 0.8A |  |  |  | CUS08F30H3FTR-ND |  |  | Toshiba Semiconductor and Storage | 757-CUS08F30H3F | CUS08F30 |  |  |  | 30V
22 | 24 | TEST_POINT | TP1, TP2, TP3, TP4, TP5, TP6, TP7, TP8, TP9, TP10, TP11, TP12, TP13, TP14, TP15, TP16, TP17, TP18, TP19, TP20, TP21, TP22 | 9 |  |  |  |  |  |  | 36-5015CT-ND |  |  | Keystone Electronics | 534-5015 | 5015
1 | 3 | TRANSISTOR_N_MOS__PMV15ENEA | Q1 | 200 |  |  |  |  |  |  | 1727-8588-1-ND |  |  | Nexperia USA Inc. | 771-PMV15ENEAR | PMV15ENEAR
1 | 3 | TVS_8V | D5 | 200 |  |  |  |  |  |  | GSOT08-E3-08TR-ND |  |  | Vishay General Semiconductor - Diodes Division | 78-GSOT08-E3-08 | GSOT08-E3-08 |  |  |  | 8V
1 | 3 | VOLTAGE_REGULATOR_ADJ_LR8_DPAK | U102 | 200 |  |  |  |  |  |  | LR8K4-GTR-ND |  |  | Microchip Technology | 689-LR8K4-G | LR8K4-G
1 | 3 | VOLTAGE_REGULATOR_SOT223_5V | U4 | 200 |  |  |  |  |  |  | 497-17240-1-ND |  |  | STMicroelectronics | 511-LDL1117S50R | LDL1117S50R

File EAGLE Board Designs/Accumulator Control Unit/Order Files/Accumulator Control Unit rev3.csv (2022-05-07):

Board Quantity | Ordering Quantity | Value | Reference | ATTRITION | CAPACITANCE | COLOR | CURRENT | DKPN | GAUGE | MANUFACTURER | MOPN | MPN | POWER | RESISTANCE | TEENSY | TOLERANCE | VOLTAGE | VOLTAGE_CONTINUOUS | VOLTAGE_MAX
1 | 3 | ADG1423 | U100 | 200 |  |  |  | ADG1423BRMZ-REEL7CT-ND |  | Analog Devices Inc. | 584-ADG1423BRMZ | ADG1423BRMZ
1 | 3 | ADM8316WBX30 | U7 | 200 |  |  |  | ADM8316WBX30ARJZR7TR-ND |  | Analog Devices Inc. | 584-M8316WBX30ARJZR7 | ADM8316WBX30ARJZR7
21 | 31 | CAPACITOR_0603_10V_0.1UF | C3, C5, C9, C10, C11, C13, C14, C15, C16, C17, C18, C19, C21, C22, C26, C27, C28, C30, C31, C34, C38 | 48 | 0.1µF |  |  | 720-1688-1-ND |  | Vishay Vitramon | 77-VJ0603Y104JXQPBC | VJ0603Y104JXQPW1BC |  |  |  | 5% | 10V
3 | 13 | CAPACITOR_0603_10V_10NF | C1, C6, C100 | 333 | 10nF |  |  | 311-4054-1-ND |  | Yageo | 603-CC603KRX7R6BB103 | CC0603KRX7R6BB103 |  |  |  | 10% | 10V
2 | 12 | CAPACITOR_0603_10V_1UF | C37, C39 | 500 | 1µF |  |  | 311-1796-1-ND |  | Yageo | 603-CC603KRX7R6BB105 | CC0603KRX7R6BB105 |  |  |  | 10% | 10V
1 | 11 | CAPACITOR_0603_10V_4.7NF | C25 | 1000 | 4.7nF |  |  | 732-7931-1-ND |  | Würth Elektronik | 710-885012206012 | 885012206012 |  |  |  | 10% | 10V
2 | 12 | CAPACITOR_0603_10V_4.7UF | C36, C103 | 500 | 4.7µF |  |  | 1276-1044-1-ND |  | Samsung Electro-Mechanics | 187-CL10A475KP8NNNC | CL10A475KP8NNNC |  |  |  | 10% | 10V
4 | 14 | CAPACITOR_0603_10V_680PF | C4, C12, C23, C32 | 250 | 680pF |  |  | 732-7757-1-ND |  | Würth Elektronik | 710-885012006013 | 885012006013 |  |  |  | 5% | 10V
6 | 16 | CAPACITOR_0603_25V_0.1UF | C2, C8, C20, C29, C35, C102 | 167 | 0.1µF |  |  | 1276-1006-1-ND |  | Samsung Electro-Mechanics | 187-CL10B104KA8NNNC | CL10B104KA8NNNC |  |  |  | 10% | 25V
2 | 12 | CAPACITOR_0603_25V_10UF | C24, C33 | 500 | 10µF |  |  | 490-7202-1-ND |  | Murata Electronics | 81-GRM188R61E106MA3D | GRM188R61E106MA73D |  |  |  | 20% | 25V
2 | 12 | CAPACITOR_0603_25V_1UF | C101, C104 | 500 | 1µF |  |  | 1276-1184-1-ND |  | Samsung Electro-Mechanics | 187-CL10B105KA8NNNC | CL10B105KA8NNNC |  |  |  | 10% | 25V
1 | 3 | CONNECTOR-12_MF_T_V_ | J5 | 200 |  |  |  |  |  | MOLEX |  | 430451214
1 | 3 | CONNECTOR-14_MF_T_V_ | J3 | 200 |  |  |  |  |  | MOLEX |  | 430451414
1 | 3 | CONNECTOR-2_MF_T_V_ | J1 | 200 |  |  |  |  |  | MOLEX |  | 436500217
1 | 3 | CONNECTOR-8_MF_T_V_ | J2 | 200 |  |  |  |  |  | MOLEX |  | 430450814
1 | 3 | CONNECTOR-8_S_S | J100 | 200 |  |  |  | S7107-ND |  | Sullins Connector Solutions |  | PPPC042LFBN-RC
1 | 3 | CONNECTOR-CAN_μF_S_RA_ | J6 | 200 |  |  |  | WM1832CT-ND |  | Molex | 538-43045-0411 | 0430450411
24 | 48 | CRIMP_MICROFIT_20-24 | O4, O5, O6, O7, O8, O9, O10, O11, O12, O13, O14, O15, O16, O17, O18, O19, O20, O21, O22, O23, O24, O25, O26, O27 | 100 |  |  |  | WM2776CT-ND | 20-24 | Molex | 538-43030-0003 | 0430300003
2 | 4 | FUSE_0603_.75A | F1, F2 | 100 |  |  | 0.75A | 507-2159-2-ND |  | Bel Fuse | 530-0686F0750-01 | 0686F0750-01 |  |  |  |  | 63V
1 | 3 | FUSE_HOLDER_MINIBLADEPTH | XF1 | 200 |  |  |  | 36-3568-ND |  | Keystone | 534-3568 | 3568
1 | 2 | FUSE_MINI_BLADE_1 | O28 | 100 |  |  |  | 2298-ANM58-1A-ND |  | OptiFuse |  | ANM58-1A
1 | 3 | JUMPER__1X02 | J4 | 200 |  |  |  | S1011EC-02-ND |  | Sullins Connector Solutions |  | PRPC002SAAN-RC
2 | 12 | LED_0603_BLUE | 5V, WATCHDOG | 500 |  | Blue |  | 754-1789-1-ND |  | Kingbright | 604-APT1608VBC/D | APT1608VBC/D
3 | 13 | LED_0603_GREEN | 3.3V, AMS_OK, TSAL_GREEN | 333 |  | Green |  | 754-1790-1-ND |  | Kingbright | 604-APT1608ZGCK | APT1608ZGCK
1 | 11 | LED_0603_ORANGE | IMD_OK | 1000 |  | Orange |  | 754-1120-1-ND |  | Kingbright | 604-APT1608SECK | APT1608SECK
4 | 14 | LED_0603_RED | 12V, PRECHARGE_OK, TEENSY_OK, TSAL_RED | 250 |  | Red |  | 754-1786-1-ND |  | Kingbright | 604-APT1608SECKJ3PRV | APT1608SECK/J3-PRV
1 | 2 | LED_0603_YELLOW | OKHS | 100 |  | Yellow |  | 754-1788-1-ND |  | Kingbright | 604-APT1608SYCK/J3-PRV | APT1608SYCK/J3-PRV
1 | 3 | LM555 | U101 | 200 |  |  |  | LM555CMX/NOPBCT-ND |  | Texas Instruments | 926-LM555CMX/NOPB | LM555CMX/NOPB
3 | 5 | LOGICGATE_AND_DCK3 | U12, U14, U16 | 67 |  |  |  | 296-SN74LVC1G08DCK3TR-ND |  | Texas Instruments | 595-SN74LVC1G08DCK3 | SN74LVC1G08DCK3
1 | 3 | LOGICGATE_BUFFER | U6 | 200 |  |  |  | 296-26604-2-ND |  | Texas Instruments | 595-SN74LVC1G34DCKT | SN74LVC1G34DCKT
1 | 3 | LTC6820 | U5 | 200 |  |  |  |  |  | Analog Devices |  | LTC6820IMS#PBF
4 | 6 | MAX7404 | U4, U10, U19, U25 | 50 |  |  |  | MAX7404CSA+-ND |  | Maxim Integrated | 700-MAX7404CSA | MAX7404CSA+
12 | 14 | OPAMP_1_CHANNEL_OPA991 | U3, U9, U11, U13, U15, U17, U18, U20, U21, U22, U23, U24 | 17 |  |  |  | 296-OPA991IDCKRCT-ND |  | Texas Instruments | 595-OPA991IDCKR | OPA991IDCKR
1 | 2 | RECEPTACLE-12_MICROFIT | O3 | 100 |  |  |  | WM1788-ND |  | Molex | 538-43025-1200 | 430251200
1 | 2 | RECEPTACLE-14_MICROFIT | O2 | 100 |  |  |  | 0430251400 |  | Molex | 538-43025-1400 | 430251400
1 | 2 | RECEPTACLE-8_MICROFIT | O1 | 100 |  |  |  | WM13210-ND |  | Molex | 538-43025-0808 | 0430250808
3 | 5 | RELAY_SOLIDSTATE_NO | U1, U2, U8 | 67 |  |  |  |  |  |  |  | AQY214EHA
5 | 15 | RESISTOR_0603_ | R4, R20, R79, R108, R110 | 200 |  |  |  | P30KBDCT-ND |  | Panasonic Electronic Components | 667-ERA-3ARB303V | ERA-3ARB303V | 0.1W | 30k |  | 0.1% |  | 54.77V | 75V
1 | 11 | RESISTOR_0603_1.4K | R58 | 1000 |  |  |  | 311-2465-1-ND |  | Yageo | 603-RT0603DRE071K4L | RT0603DRE071K4L | 0.1W | 1.4K |  | 0.5% |  | 75V | 75V
4 | 14 | RESISTOR_0603_10 | R13, R18, R103, R104 | 250 |  |  |  | 311-10.0HRCT-ND |  | Yageo | 603-RC0603FR-0710RL | RC0603FR-0710RL | 0.1W | 10 |  | 1% |  | 1V | 75V
2 | 12 | RESISTOR_0603_10.2K | R41, R48 | 500 |  |  |  | P10.2KDBCT-ND |  | Panasonic Electronic Components | 667-ERA-3AEB1022V | ERA-3AEB1022V | 0.1W | 10.2k |  | 0.1% |  | 31.94V | 75V
4 | 14 | RESISTOR_0603_10.5K | R65, R68, R72, R76 | 250 |  |  |  | P10.5KDBCT-ND |  | Panasonic Electronic Components | 677-ERA-3AEB1052V | ERA-3AEB1052V | 0.1W | 10.5k |  | 0.1% |  | 32.40V | 75V
27 | 37 | RESISTOR_0603_10K | R6, R12, R14, R17, R22, R26, R27, R29, R30, R37, R42, R43, R44, R50, R52, R55, R59, R69, R71, R73, R77, R81, R82, R100, R101, R102, R106 | 37 |  |  |  | 311-10.0KHRCT-ND |  | Yageo | 603-RC0603FR-0710KL | RC0603FR-0710KL | 0.1W | 10k |  | 1% |  | 31.62V | 75V
1 | 11 | RESISTOR_0603_11.3K | R70 | 1000 |  |  |  | P11.3KDBCT-ND |  | Panasonic Electronic Components | 667-ERA-3AEB1132V | ERA-3AEB1132V | 0.1W | 11.3k |  | 0.1% |  | 33.62V | 75V
7 | 17 | RESISTOR_0603_11.5K | R38, R51, R53, R66, R67, R74, R75 | 143 |  |  |  | P11.5KDBCT-ND |  | Panasonic Electronic Components | 667-ERA-3AEB1152V | ERA-3AEB1152V | 0.1W | 11.5k |  | 0.1% |  | 33.91V | 75V
1 | 11 | RESISTOR_0603_120 | R1 | 1000 |  |  |  | P120DBCT-ND |  | Panasonic Electronic Components | 667-ERA-3AEB121V | ERA-3AEB121V | 0.1W | 120 |  | 0.1% |  | 3.46V | 75V
7 | 17 | RESISTOR_0603_12K | R5, R23, R31, R56, R78, R80, R107 | 143 |  |  |  | 311-12.0KHRCT-ND |  | Yageo | 603-RC0603FR-0712KL | RC0603FR-0712KL | 0.1W | 12k |  | 1% |  | 34.64V | 75V
1 | 11 | RESISTOR_0603_15K | R21 | 1000 |  |  |  | P15KBDCT-ND |  | Panasonic Electronic Components | 667-ERA-3ARB153V | ERA-3ARB153V | 0.1W | 15k |  | 0.1% |  | 38.73V | 75V
1 | 11 | RESISTOR_0603_18.7K | R109 | 1000 |  |  |  | 311-18.7KHRCT-ND |  | Yageo | 603-RC0603FR-0718K7L | RC0603FR-0718K7L | 0.1W | 18.7k |  | 1% |  | 43.24V | 75V
9 | 19 | RESISTOR_0603_1K | R3, R9, R10, R11, R16, R19, R24, R25, R57 | 111 |  |  |  | 311-1.00KHRCT-ND |  | Yageo | 603-RC0603FR-071KL | RC0603FR-071KL | 0.1W | 1k |  | 1% |  | 10.00V | 75V
1 | 11 | RESISTOR_0603_2.2K | R15 | 1000 |  |  |  | 13-RC0603DR-072K2LCT-ND |  | Yageo | 603-RC0603DR-072K2L | RC0603DR-072K2L | 0.1W | 2.2k |  | 0.5% |  | 75V | 75V
1 | 11 | RESISTOR_0603_215K | R46 | 1000 |  |  |  | P215KDBCT-ND |  | Panasonic Electronic Components | 667-ERA-3AEB2153V | ERA-3AEB2153V | 0.1W | 215k |  | 0.1% |  | 75V | 75V
7 | 17 | RESISTOR_0603_2K | R2, R7, R8, R32, R33, R61, R62 | 143 |  |  |  | P2.0KBDCT-ND |  | Panasonic Electronic Components | 667-ERA-3ARB202V | ERA-3ARB202V | 0.1W | 2k |  | 0.1% |  | 14.14V | 75V
2 | 12 | RESISTOR_0603_4.12K | R49, R63 | 500 |  |  |  | P4.12KDBCT-ND |  | Panasonic Electronic Components | 667-ERA-3AEB4121V | ERA-3AEB4121V | 0.1W | 4.12k |  | 0.1% |  | 20.30V | 75V
1 | 11 | RESISTOR_0603_43K | R105 | 1000 |  |  |  | 311-43.0KHRCT-ND |  | Yageo | 603-RC0603FR-0743KL | RC0603FR-0743KL | 0.1W | 43k |  | 1% |  | 65.57V | 75V
3 | 13 | RESISTOR_0603_470 | R28, R34, R35 | 333 |  |  |  | P470BYCT-ND |  | Panasonic Electronic Components | 667-ERJ-PA3F4700V | ERJ-PA3F4700V | 0.25W | 470 |  | 1% |  | 10.84V | 150V
2 | 12 | RESISTOR_0603_60.4 | R36, R60 | 500 |  |  |  | 311-60.4HRCT-ND |  | Yageo | 603-RC0603FR-0760R4L | RC0603FR-0760R4L | 0.1W | 60.4 |  | 1% |  | 2.48V | 75V
1 | 11 | RESISTOR_0603_84.5K | R39 | 1000 |  |  |  | P84.5KDBCT-ND |  | Panasonic Electronic Components | 667-ERA-3AEB8452V | ERA-3AEB8452V | 0.1W | 84.5k |  | 0.1% |  | 75V | 75V
5 | 15 | RESISTOR_0603_DNP | R40, R45, R47, R54, R64 | 200 |  |  |  |  |  |  |  |  |  | DNP
1 | 3 | TCAN1051HQV-Q1 | U27 | 200 |  |  |  | 296-49935-1-ND |  | Texas Instruments | 595-TCAN1051HGVDQ1 | TCAN1051HGVDRQ1
1 | 3 | TEENSY_4.0 | A2 | 200 |  |  |  |  |  |  |  |  |  |  | 4.0
17 | 19 | TEST_POINT | BSPD_CURRENT, CURRENT_REF, CURRENT_SENSE, PACK+_OUT_TEST, PRECHARGE_OK_TEST, TD+, TD-, TP_3.3V, TP_5V, TP_12V, TP_AMS_OK, TP_GND, TP_IMD_OK, TP_TSAL_GREEN, TP_TSAL_RED, TS+_OUT_TEST, WATCHDOG_OK | 12 |  |  |  | 36-5015CT-ND |  | Keystone Electronics | 534-5015 | 5015
1 | 3 | TRANSFORMER_HM2112ZNLT_AIRGAP | T1 | 200 |  |  |  | 1840-1036-1-ND |  | Pulse Electronics | 673-HM2112ZNLT | HM2112ZNLT
4 | 6 | TRANSISTOR_N_MOS__PMV15ENEA | Q1, Q2, Q100, Q101 | 50 |  |  |  | 1727-8588-1-ND |  | Nexperia USA Inc. | 771-PMV15ENEAR | PMV15ENEAR
8 | 10 | TVS_15V | D3, D7, D8, D9, D10, D11, D100, D101 | 25 |  |  |  | GSOT15-E3-08CT-ND |  | Vishay General Semiconductor - Diodes Division | 78-GSOT15-E3-08 | GSOT15-E3-08 |  |  |  |  | 15V
2 | 4 | TVS_8V | D2, D4 | 100 |  |  |  | GSOT08-E3-08-ND |  | Vishay General Semiconductor - Diodes Division | 78-GSOT08-E3-08 | GSOT08-E3-08 |  |  |  |  | 8V
1 | 3 | VOLTAGE_REGULATOR_MODULE_OKI-78SR_5V | A1 | 200 |  |  |  | 811-2196-5-ND |  | Murata Power Solutions Inc. | 580-OKI78SR5/1.5W36C | OKI-78SR-5/1.5-W36-C
1 | 3 | VOLTAGE_REGULATOR_SOT223_3.3V | U26 | 200 |  |  |  | 497-17239-1-ND |  | STMicroelectronics | 511-LDL1117S33R | LDL1117S33R

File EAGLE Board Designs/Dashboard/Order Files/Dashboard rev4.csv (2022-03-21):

Board Quantity | Ordering Quantity | Value | Reference | ALT_DKPN | ALT_MANUFACTURER | ALT_MOPN | ALT_MPN | ATTRITION | CAPACITANCE | COLOR | CURRENT | CURRENT_RATED | CURRENT_SATURATION | DCR | DKPN | FREQUENCY | FUSE_TYPE | GAUGE | INDUCTANCE | LOAD_CAPACITANCE | MANUFACTURER | MOPN | MPN | POWER | RESISTANCE | SHUNT_CAPACITANCE | TOLERANCE | VIN | VOLTAGE | VOLTAGE_CONTINUOUS | VOLTAGE_MAX | VOLUME | VOUT
1 | 3 | ATMEGA328P-AU | U1 |  |  |  |  | 200 |  |  |  |  |  |  | ATMEGA328P-AURCT-ND |  |  |  |  |  | Microchip Technology | 556-ATMEGA328P-AU | ATMEGA328P-AU
1 | 3 | BUZZER_3_PIN_CPT-3011C-120 | LS100 |  |  |  |  | 200 |  |  |  |  |  |  | 102-3762-ND | 3kHz |  |  |  |  | CUI Devices | 490-CPT-3011C-120 | CPT-3011C-120 |  |  |  |  |  | 12V |  |  | 85dB
12 | 22 | CAPACITOR_0603_10V_0.1UF | C4, C6, C7, C8, C9, C10, C11, C12, C14, C15, C16, C17 |  |  |  |  | 83 | 0.1µF |  |  |  |  |  | 720-1688-1-ND |  |  |  |  |  | Vishay Vitramon | 77-VJ0603Y104JXQPBC | VJ0603Y104JXQPW1BC |  |  |  | 5% |  | 10V
4 | 14 | CAPACITOR_0603_10V_15PF | C1, C2, C18, C19 |  |  |  |  | 250 | 15pF |  |  |  |  |  | 720-VJ0603A150FXQPW1BCCT-ND |  |  |  |  |  | Vishay Vitramon | 77-VJ0603A150FXQPBC | VJ0603A150FXQPW1BC |  |  |  | 1% |  | 10V
1 | 11 | CAPACITOR_0603_10V_4.7NF | C13 |  |  |  |  | 1000 | 4.7nF |  |  |  |  |  | 732-7931-1-ND |  |  |  |  |  | Würth Elektronik | 710-885012206012 | 885012206012 |  |  |  | 10% |  | 10V
1 | 11 | CAPACITOR_0603_25V_0.1UF | C5 |  |  |  |  | 1000 | 0.1µF |  |  |  |  |  | 1276-1006-1-ND |  |  |  |  |  | Samsung Electro-Mechanics | 187-CL10B104KA8NNNC | CL10B104KA8NNNC |  |  |  | 10% |  | 25V
1 | 11 | CAPACITOR_0603_25V_1.2NF | C3 |  |  |  |  | 1000 | 1.2nF |  |  |  |  |  | 311-4079-2-ND |  |  |  |  |  | YAGEO | 603-CC603KRX7R8BB122 | CC0603KRX7R8BB122 |  |  |  | 10% |  | 25V
1 | 3 | CONNECTOR-6_μF_S_RA_ | J2 |  |  |  |  | 200 |  |  |  |  |  |  | WM1833CT-ND |  |  |  |  |  | Molex | 538-43045-0611 | 0430450611
1 | 3 | CONNECTOR-8_μF_S_RA_ | J4 |  |  |  |  | 200 |  |  |  |  |  |  | WM1834CT-ND |  |  |  |  |  | Molex | 538-43045-0811 | 0430450811
1 | 3 | CONNECTOR-AVR-ISP_2X05_SMD | J1 |  |  |  |  | 200 |  |  |  |  |  |  | S2351E-05-ND |  |  |  |  |  | Sullins Connector Solutions |  | GBC05DABN-M30
1 | 3 | CONNECTOR-CAN_μF_S_RA_ | J3 |  |  |  |  | 200 |  |  |  |  |  |  | WM1832CT-ND |  |  |  |  |  | Molex | 538-43045-0411 | 0430450411
18 | 36 | CRIMP_MICROFIT_20-24 | O6, O7, O8, O9, O10, O11, O12, O13, O14, O15, O16, O17, O18, O19, O20, O21, O22, O23 |  |  |  |  | 100 |  |  |  |  |  |  | WM2776CT-ND |  |  | 20-24 |  |  | Molex | 538-43030-0003 | 0430300003
2 | 4 | CRYSTAL_16MHZ | X1, X2 |  |  |  |  | 100 |  |  |  |  |  |  | XC2566CT-ND | 16 MHz |  |  |  | 10pF | TXC CORPORATION | 520-160-10-42-CKMT | ECS-160-10-42-CKM-TR |  |  | 2 - 5 pF
1 | 3 | FUSE_HOLDER_MINIBLADESMD | XF1 |  |  |  |  | 200 |  |  |  |  |  |  | 36-3588-ND |  | MINI 297 |  |  |  | Keystone Electronics | 534-3588 | 3588
1 | 2 | FUSE_MINI_BLADE_2 | O4 |  |  |  |  | 100 |  |  | 2A |  |  |  | F986-ND |  | MINI 297 |  |  |  | Littelfuse Inc. | 576-0297002.WXNV | 0297002.WXNV
1 | 3 | INDUCTOR_LQM18DH100M70_10UH | L1 |  |  |  |  | 200 |  |  |  | 300mA | 100mA | 1.37Ω | 490-LQM18DH100M70LTR-ND |  |  |  | 10µH |  | Murata Electronics | 81-LQM18DH100M70L | LQM18DH100M70L |  |  |  | 20%
1 | 11 | JUMPER_0603_ | J5 |  |  |  |  | 1000 |  |  |  |  |  |  | 13-RC0603FR-130RLTR-ND |  |  |  |  |  | YAGEO | 603-RC0603FR-130RL | RC0603FR-130RL
1 | 11 | LED_0603_BLUE | D7 |  |  |  |  | 1000 |  | Blue |  |  |  |  | 754-1789-1-ND |  |  |  |  |  | Kingbright | 604-APT1608VBC/D | APT1608VBC/D
1 | 11 | LED_0603_GREEN | D6 |  |  |  |  | 1000 |  | Green |  |  |  |  | 754-1790-1-ND |  |  |  |  |  | Kingbright | 604-APT1608ZGCK | APT1608ZGCK
1 | 11 | LED_0603_ORANGE | D5 |  |  |  |  | 1000 |  | Orange |  |  |  |  | 754-1120-1-ND |  |  |  |  |  | Kingbright | 604-APT1608SECK | APT1608SECK
3 | 5 | LED_2835_AMBER | D1, D2, D106 |  |  |  |  | 67 |  | Amber |  |  |  |  |  |  |  |  |  |  | Lumileds | 997-L128PCA10350 | L128-PCA1003500000
1 | 3 | LED_2835_BLUE | D105 |  |  |  |  | 200 |  | Blue |  |  |  |  |  |  |  |  |  |  | Lumileds | 997-L128BLU10350 | L128-BLU1003500000
2 | 4 | LED_2835_GREEN | D8, D104 |  |  |  |  | 100 |  | Green |  |  |  |  |  |  |  |  |  |  | Lumileds | 997-L128GRN10350 | L128-GRN1003500000
2 | 4 | LED_2835_RED | D100, D107 |  |  |  |  | 100 |  | Red |  |  |  |  |  |  |  |  |  |  | Lumileds | 997-L128RED10350 | L128-RED1003500000
1 | 3 | LED_2835_RED-ORANGE | D3 |  |  |  |  | 200 |  | Red-Orange |  |  |  |  |  |  |  |  |  |  | Lumileds | 997-L128RNG10350 | L128-RNG1003500000
1 | 3 | LED_7_SEGMENT_BLUE_DSM7TA | D101 |  |  |  |  | 200 |  | Blue |  |  |  |  | DSM7TA56106TTR-ND |  |  |  |  |  | Visual Communications Company | 593-DSM7TA56106T | DSM7TA56106T
2 | 4 | LOGICGATE_INVERTER_DCK3 | U6, U7 |  |  |  |  | 100 |  |  |  |  |  |  | 296-SN74LVC1G04DCK3TR-ND |  |  |  |  |  | Texas Instruments | 595-SN74LVC1G04DCK3 | SN74LVC1G04DCK3
1 | 3 | MCP23S08 | U3 |  |  |  |  | 200 |  |  |  |  |  |  | MCP23S08-E/SS-ND |  |  |  |  |  | Microchip Technology | 579-MCP23S08-E/SS | MCP23S08-E/SS
1 | 3 | MCP2515 | U5 |  |  |  |  | 200 |  |  |  |  |  |  | MCP2515-E/ST-ND |  |  |  |  |  | Microchip Technology | 579-MCP2515-E/ST | MCP2515-E/ST
1 | 3 | MCP2562FD | U4 | MCP2562-E/SN-ND | Microchip Technology | 579-MCP2562-E/SN | MCP2562-E/SN | 200 |  |  |  |  |  |  | MCP2562FD-E/SN-ND |  |  |  |  |  | Microchip Technology | 579-MCP2562FD-E/SN | MCP2562FD-E/SN
1 | 3 | OKL-T/1-W12N-COKL | A1 |  |  |  |  | 200 |  |  |  |  |  |  | 811-2260-2-ND |  |  |  |  |  | Murata Power Solutions Inc. | 580-OKL-T/1-W12N-C | OKL-T/1-W12N-C |  |  |  |  | 12V |  |  |  |  | 5V
1 | 3 | RE46C100 | U2 |  |  |  |  | 200 |  |  |  |  |  |  | RE46C100S8TFTR-ND |  |  |  |  |  | Microchip Technology | 579-RE46C100S8TF | RE46C100S8TF
1 | 2 | RECEPTACLE-4_MICROFIT | O1 |  |  |  |  | 100 |  |  |  |  |  |  | WM11225-ND |  |  |  |  |  | Molex | 538-43025-0408 | 0430250408
1 | 2 | RECEPTACLE-6_MICROFIT | O2 |  |  |  |  | 100 |  |  |  |  |  |  | WM13209-ND |  |  |  |  |  | Molex | 538-43025-0608 | 0430250608
1 | 2 | RECEPTACLE-8_MICROFIT | O3 |  |  |  |  | 100 |  |  |  |  |  |  | WM13210-ND |  |  |  |  |  | Molex | 538-43025-0808 | 0430250808
1 | 11 | RESISTOR_0603_1.5M | R10 |  |  |  |  | 1000 |  |  |  |  |  |  | 311-1.50MHRCT-ND |  |  |  |  |  | Yageo | 603-RC0603FR-071M5L | RC0603FR-071M5L | 0.1W | 1.5M |  | 1% |  |  | 75V | 75V
1 | 11 | RESISTOR_0603_10 | R27 |  |  |  |  | 1000 |  |  |  |  |  |  | 311-10.0HRCT-ND |  |  |  |  |  | Yageo | 603-RC0603FR-0710RL | RC0603FR-0710RL | 0.1W | 10 |  | 1% |  |  | 1V | 75V
1 | 11 | RESISTOR_0603_100 | R9 |  |  |  |  | 1000 |  |  |  |  |  |  | 311-100HRCT-ND |  |  |  |  |  | Yageo | 603-RC0603FR-07100RL | RC0603FR-07100RL | 0.1W | 100 |  | 1% |  |  | 3.16V | 75V
4 | 14 | RESISTOR_0603_10K | R11, R13, R21, R28 |  |  |  |  | 250 |  |  |  |  |  |  | 311-10.0KHRCT-ND |  |  |  |  |  | Yageo | 603-RC0603FR-0710KL | RC0603FR-0710KL | 0.1W | 10k |  | 1% |  |  | 31.62V | 75V
7 | 17 | RESISTOR_0603_15 | R1, R8, R12, R14, R17, R23, R26 |  |  |  |  | 143 |  |  |  |  |  |  | 541-15.0STR-ND |  |  |  |  |  | Vishay Dale | 71-CRCW060315R0FKEAH | CRCW060315R0FKEAHP | 0.33W | 15 |  | 1% |  |  | 2.22V | 75V
1 | 11 | RESISTOR_0603_150K | R15 |  |  |  |  | 1000 |  |  |  |  |  |  | P150KDBCT-ND |  |  |  |  |  | Panasonic Electronic Components | 667-ERA-3AEB154V | ERA-3AEB154V | 0.1W | 150k |  | 1% |  |  | 75V | 75V
1 | 11 | RESISTOR_0603_2.18K | R19 |  |  |  |  | 1000 |  |  |  |  |  |  | 13-RT0805BRD072K18LTR-ND |  |  |  |  |  | YAGEO | 603-RT0805BRD072K18L | RT0805BRD072K18L | 0.125W | 2.18k |  | 0.1% |  |  | 16.51V | 150V
4 | 14 | RESISTOR_0603_30K | R2, R3, R4, R25 |  |  |  |  | 250 |  |  |  |  |  |  | P30KBDCT-ND |  |  |  |  |  | Panasonic Electronic Components | 667-ERA-3ARB303V | ERA-3ARB303V | 0.1W | 30k |  | 0.1% |  |  | 54.77V | 75V
4 | 14 | RESISTOR_0603_43K | R5, R6, R7, R24 |  |  |  |  | 250 |  |  |  |  |  |  | 311-43.0KHRCT-ND |  |  |  |  |  | Yageo | 603-RC0603FR-0743KL | RC0603FR-0743KL | 0.1W | 43k |  | 1% |  |  | 65.57V | 75V
2 | 12 | RESISTOR_0603_60.4 | R18, R20 |  |  |  |  | 500 |  |  |  |  |  |  | 311-60.4HRCT-ND |  |  |  |  |  | Yageo | 603-RC0603FR-0760R4L | RC0603FR-0760R4L | 0.1W | 60.4 |  | 1% |  |  | 2.48V | 75V
2 | 12 | RESISTOR_0805_22 | R16, R22 |  |  |  |  | 500 |  |  |  |  |  |  | P16066TR-ND |  |  |  |  |  | Panasonic Electronic Components | 667-ERJ-P06F22R0V | ERJ-P06F22R0V | 0.5W | 22 |  | 1% |  |  | 3.32V | 400V
2 | 4 | RESISTOR_NETWORK_4_10 | RN2, RN8 |  |  |  |  | 100 |  |  |  |  |  |  | CAT16-100J4LFCT-ND |  |  |  |  |  | Bourns Inc. | 652-CAT16-100J4LF | CAT16-100J4LF | 1/16W | 10 |  | 5% |  | 50V
2 | 4 | RESISTOR_NETWORK_4_10K | RN1, RN4 |  |  |  |  | 100 |  |  |  |  |  |  | YAG3410CT-ND |  |  |  |  |  | Yageo | 603-TC164-FR-0710KL | TC164-FR-0710KL | 1/16W | 10K |  | 1% |  | 50V
2 | 4 | RESISTOR_NETWORK_4_160 | RN5, RN7 |  |  |  |  | 100 |  |  |  |  |  |  | YC164J-160CT-ND |  |  |  |  |  | Yageo | 603-YC164-JR-07160RL | YC164-JR-07160RL | 1/16W | 160 |  | 5% |  | 50V
1 | 3 | RESISTOR_NETWORK_4_1K | RN6 |  |  |  |  | 200 |  |  |  |  |  |  | 13-YC164-FR-071KLCT-ND |  |  |  |  |  | Yageo | 603-YC164-FR-071KL | YC164-FR-071KL | 1/16W | 1k |  | 1% |  | 50V
7 | 9 | TEST_POINT | TP1, TP2, TP3, TP4, TP5, TP6, TP7 |  |  |  |  | 29 |  |  |  |  |  |  | 36-5015CT-ND |  |  |  |  |  | Keystone Electronics | 534-5015 | 5015
9 | 11 | TRANSISTOR_N_MOS__PMV15ENEA | Q1, Q2, Q3, Q4, Q5, Q6, Q7, Q8, Q9 |  |  |  |  | 22 |  |  |  |  |  |  | 1727-8588-1-ND |  |  |  |  |  | Nexperia USA Inc. | 771-PMV15ENEAR | PMV15ENEAR
1 | 3 | TVS_15V | D4 |  |  |  |  | 200 |  |  |  |  |  |  | GSOT15-E3-08CT-ND |  |  |  |  |  | Vishay General Semiconductor - Diodes Division | 78-GSOT15-E3-08 | GSOT15-E3-08 |  |  |  |  |  | 15V
2 | 4 | TVS_ARRAY_5V | DN1, DN2 |  |  |  |  | 100 |  |  |  |  |  |  | 112-VESD05A5-06G-G3-08CT-ND |  |  |  |  |  | Vishay General Semiconductor - Diodes Division | 78-VESD05A5-06G-G308 | VESD05A5-06G-G3-08 |  |  |  |  |  | 5V

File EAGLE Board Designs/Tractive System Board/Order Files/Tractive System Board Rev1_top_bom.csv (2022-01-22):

Comment | Designator | Footprint | LCSC Part #
CAPACITOR_0603_10V_0.1UF | C10 | 0603-CAP
CAPACITOR_0603_10V_1UF | C38 C39 C40 C45 C46 C47 | 0603-CAP
CAPACITOR_0603_10V_10NF | C35 C48 C49 | 0603-CAP
CAPACITOR_0603_25V_0.1UF | C37 | 0603-CAP
CAPACITOR_0603_25V_1UF | C36 | 0603-CAP
CAPACITOR_0805_25V_22UF | C34 | 0805-CAP
CAPACITOR_1206_250V_0.1UF | C3 C4 | 1206-CAP
CAPACITOR_2220_250V_1UF | C31 C32 | 2220-CAP
CAPACITOR_2220_630V_0.1UF | C1 C2 | 2220-CAP
CAPACITOR_2220_630V_1UF | C24 C25 C30 | 2220-CAP
FUSE_0885_1.25 | F2 F6 | 0885
INDUCTOR_PA4334_ | L4 | PA4334
INDUCTOR_SRU1048_330UH | L6 | SRU1048
INDUCTOR_WELMHI_ | L5 | WE-LMHI
ISO224B_AIRGAP | U18 | SOIC-08(WIDE 0.295")-AIRGAP
ISO224B_AIRGAP | U19 | SOIC-08(WIDE 0.295")-AIRGAP
LED_0603_BLUE | D9 D11 D13 | 0603-LED
LED_0603_GREEN | D4 | 0603-LED
LED_0603_ORANGE | D2 | 0603-LED
LED_0603_RED | D6 | 0603-LED
LED_0603_WHITE | D5 D12 | 0603-LED
LED_0603_YELLOW | D3 | 0603-LED
LOGICGATE_INVERTER_DCKR | U15 | SC-70-5
LTC3639 | U16 | MSE16(12)
RELAY_SOLIDSTATE_NO_AG | U$1 | DIP-4_AIRGAP
RESISTOR_0603_1.62 | R31 | 0603-RES
RESISTOR_0603_1K | R28 R29 R30 R32 R35 R36 R52 R53 R54 R55 R63 | 0603-RES
RESISTOR_0603_5.9K | R1 R2 | 0603-RES
RESISTOR_0603_10 | R37 | 0603-RES
RESISTOR_0603_10K | R38 R47 | 0603-RES
RESISTOR_0603_33.2K | R49 R50 | 0603-RES
RESISTOR_0805_1 | R26 | 0805-RES
RESISTOR_0805_12.4 | R27 | 0805-RES
RESISTOR_0805_365K | R6 R7 R8 R9 R16 R17 R18 R19 | 0805-RES
RESISTOR_GND_1.24K | R39 | B20
RESISTOR_GND_10K | R40 R41 R42 | B20
SCHOTTKY | D10 | CLP1608-2L
TEST_POINT | TP1 TP2 TP3 TP4 TP5 TP6 TP7 TP8 TP9 TP10 TP11 TP12 TP13 TP14 TP15 TP16 TP18 TP19 TP20 | MICRO_MINIATURE
TRANSISTOR_N_MOS__PMV15ENEA | Q2 | SOT-23
TVS_8V | D1 | SOT-23
VOLTAGE_REGULATOR_SOT223_5V | U2 | SOT223

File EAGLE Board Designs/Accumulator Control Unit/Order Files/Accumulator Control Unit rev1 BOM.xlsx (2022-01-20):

Qty | Value | Device | Package | Parts | Description | CAPACITANCE | COLOR | CURRENT | DKPN | MANUFACTURER | MOPN | MPN | POWER | RESET_VOLTAGE | RESISTANCE | TOLERANCE | VOLTAGE | VOLTAGE_CONTINUOUS | VOLTAGE_MAX | Column1
1 | ADG1423 | ADG1423 | MSOP-10 | U2 | ADG1423 Form-A/Form-C Analog Switch |  |  |  | ADG1423BRMZ-REEL7CT-ND | Analog Devices Inc. | 584-ADG1423BRMZ | ADG1423BRMZ
1 | ADM823 | ADM823 | SC-70-5 | U6 | ADM823 Watchdog |  |  |  | 505-ADM823TYKSZ-R7CT-ND | Analog Devices Inc. | 584-ADM823TYKSZ-R7 | ADM823TYKSZ-R7 |  | 3.08
24 | CAPACITOR_0603_10V_0.1UF | CAPACITOR_0603_10V_0.1UF | 0603-CAP | C11, C12, C13, C14, C15, C16, C20, C22, C23, C24, C25, C26, C27, C29, C30, C31, C35, C36, C39, C40, C47, C48, C51, C52 | Capacitor, Non-Polarized | 0.1µF |  |  | 720-1688-1-ND | Vishay Vitramon | 77-VJ0603Y104JXQPBC | VJ0603Y104JXQPW1BC |  |  |  | 0.05 | 10V
2 | CAPACITOR_0603_10V_10NF | CAPACITOR_0603_10V_10NF | 0603-CAP | C4, C33 | Capacitor, Non-Polarized | 10nF |  |  | 311-4054-1-ND | Yageo | 603-CC603KRX7R6BB103 | CC0603KRX7R6BB103 |  |  |  | 0.1 | 10V
1 | CAPACITOR_0603_10V_15PF | CAPACITOR_0603_10V_15PF | 0603-CAP | C34 | Capacitor, Non-Polarized | 15pF |  |  | 720-VJ0603A150FXQPW1BCCT-ND | Vishay Vitramon | 77-VJ0603A150FXQPBC | VJ0603A150FXQPW1BC |  |  |  | 0.01 | 10V
2 | CAPACITOR_0603_10V_1UF | CAPACITOR_0603_10V_1UF | 0603-CAP | C9, C32 | Capacitor, Non-Polarized | 1µF |  |  | 311-1796-1-ND | Yageo | 603-CC603KRX7R6BB105 | CC0603KRX7R6BB105 |  |  |  | 0.1 | 10V
2 | CAPACITOR_0603_10V_4.7UF | CAPACITOR_0603_10V_4.7UF | 0603-CAP | C5, C10 | Capacitor, Non-Polarized | 4.7µF |  |  | 1276-1044-1-ND | Samsung Electro-Mechanics | 187-CL10A475KP8NNNC | CL10A475KP8NNNC |  |  |  | 0.1 | 10V
4 | CAPACITOR_0603_10V_680PF | CAPACITOR_0603_10V_680PF | 0603-CAP | C43, C45, C49, C53 | Capacitor, Non-Polarized | 680pF |  |  | 732-7757-1-ND | Würth Elektronik | 710-885012006013 | 885012006013 |  |  |  | 0.05 | 10V
6 | CAPACITOR_0603_25V_0.1UF | CAPACITOR_0603_25V_0.1UF | 0603-CAP | C7, C8, C28, C37, C46, C50 | Capacitor, Non-Polarized | 0.1µF |  |  | 1276-1006-1-ND | Samsung Electro-Mechanics | 187-CL10B104KA8NNNC | CL10B104KA8NNNC |  |  |  | 0.1 | 25V
2 | CAPACITOR_0603_25V_10UF | CAPACITOR_0603_25V_10UF | 0603-CAP | C1, C2 | Capacitor, Non-Polarized | 10µF |  |  | 490-7202-1-ND | Murata Electronics | 81-GRM188R61E106MA3D | GRM188R61E106MA73D |  |  |  | 0.2 | 25V
2 | CAPACITOR_0603_25V_1UF | CAPACITOR_0603_25V_1UF | 0603-CAP | C3, C6 | Capacitor, Non-Polarized | 1µF |  |  | 1276-1184-1-ND | Samsung Electro-Mechanics | 187-CL10B105KA8NNNC | CL10B105KA8NNNC |  |  |  | 0.1 | 25V
1 | CONNECTOR-12_MF_T_V_ | CONNECTOR-12_MF_T_V_ | MOLEX_MICROFIT_PTH_VERTICAL_12_DUAL | J5 | 12 pin connector |  |  |  |  | MOLEX |  | 430451214
1 | CONNECTOR-14_MF_T_V_ | CONNECTOR-14_MF_T_V_ | MOLEX_MICROFIT_PTH_VERTICAL_14_DUAL | J6 | 14 pin connector |  |  |  |  | MOLEX |  | 430451414
1 | CONNECTOR-2_MF_T_V_ | CONNECTOR-2_MF_T_V_ | MOLEX_MICROFIT_PTH_VERTICAL_02_SINGLE | J4 | 2 Pin Connector |  |  |  |  | MOLEX |  | 436500217
2 | CONNECTOR-8_MF_T_V_ | CONNECTOR-8_MF_T_V_ | MOLEX_MICROFIT_PTH_VERTICAL_08_DUAL | J2, J3 | 8 Pin Connector |  |  |  |  | MOLEX |  | 430450814
1 | CONNECTOR-CAN_MF_T_V_ | CONNECTOR-CAN_MF_T_V_ | MOLEX_MICROFIT_PTH_VERTICAL_04_DUAL | J1 | HyTech CAN Connector |  |  |  |  | Molex |  | 430450414
1 | FUSE_MINI-BLADE_1A | FUSE_MINI-BLADE_1A | MINI-BLADE_FUSE_HOLDER | F1 | Fuse |  |  | 1A
1 | LED_0603_BLUE | LED_0603_BLUE | 0603-LED | 5V | LED |  | Blue |  | 754-1789-1-ND | Kingbright | 604-APT1608VBC/D | APT1608VBC/D
4 | LED_0603_GREEN | LED_0603_GREEN | 0603-LED | 3.3V, AMS_OK, D2, D10 | LED |  | Green |  | 754-1790-1-ND | Kingbright | 604-APT1608ZGCK | APT1608ZGCK
1 | LED_0603_ORANGE | LED_0603_ORANGE | 0603-LED | IMD_OK | LED |  | Orange |  | 754-1120-1-ND | Kingbright | 604-APT1608SECK | APT1608SECK
4 | LED_0603_RED | LED_0603_RED | 0603-LED | 12V, D3, D6, D14 | LED |  | Red |  | 754-1786-1-ND | Kingbright | 604-APT1608SECKJ3PRV | APT1608SECK/J3-PRV
1 | LED_0603_YELLOW | LED_0603_YELLOW | 0603-LED | D11 | LED |  | Yellow |  | 754-1788-1-ND | Kingbright | 604-APT1608SYCK/J3-PRV | APT1608SYCK/J3-PRV
1 | LM555 | LM555 | SOIC-08(NARROW,0.15)" | U3 | **555 Precision Timer |  |  |  | LM555CMX/NOPBCT-ND | Texas Instruments | 926-LM555CMX/NOPB | LM555CMX/NOPB
3 | LOGICGATE_AND_DCK3 | LOGICGATE_AND_DCK3 | SC-70-5 | U8, U11, U15 | AND Gate |  |  |  | 296-SN74LVC1G08DCK3TR-ND | Texas Instruments | 595-SN74LVC1G08DCK3 | SN74LVC1G08DCK3
1 | LTC6820 | LTC6820 | MSOP-16 | U5 | LTC6820 isoSPI Isolated Communications Interface |  |  |  |  | Analog Devices |  | LTC6820IMS#PBF
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

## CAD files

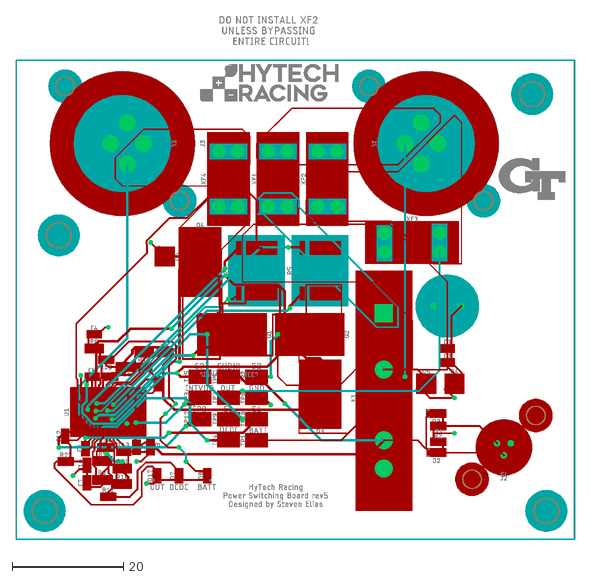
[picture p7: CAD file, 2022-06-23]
EAGLE Board Designs/Power Switching Board/Order Files/Power Switching Circuit rev5.dxf
100.5 x 94.1

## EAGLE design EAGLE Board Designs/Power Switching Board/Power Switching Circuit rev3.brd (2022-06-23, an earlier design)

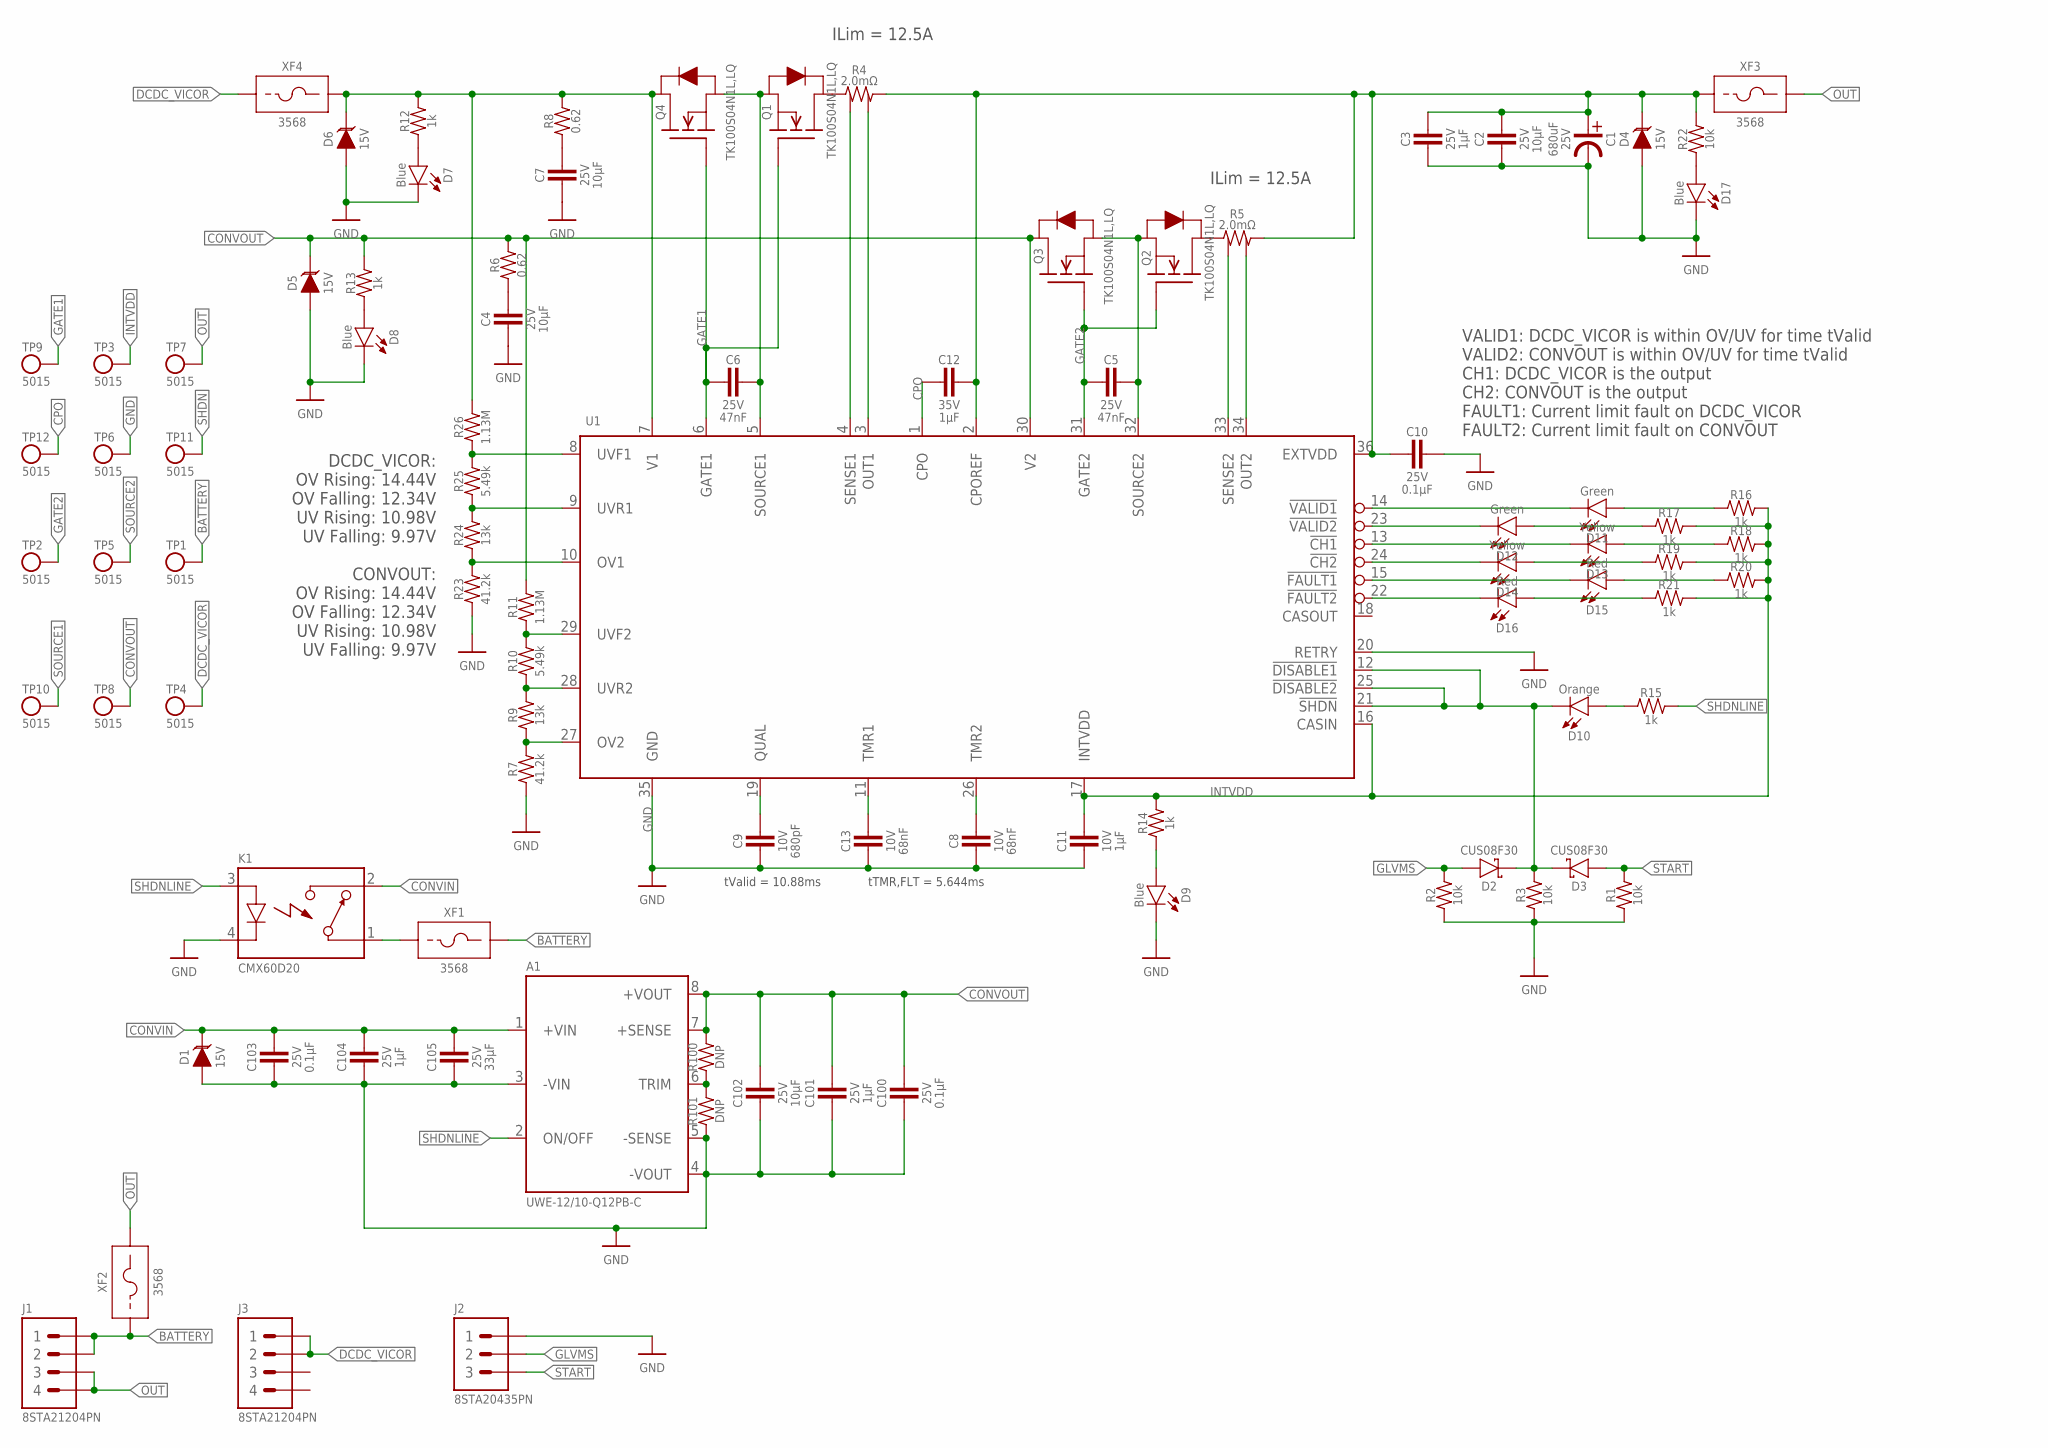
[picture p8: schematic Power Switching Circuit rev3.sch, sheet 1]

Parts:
A1: UWE-12/10-Q12PB-C; UWE-*
C1: EEUFP1E681; EEUFP1E*
C2, C4, C7, C102: CAPACITOR_0603_25V_10UF; 0603-CAP
C3, C101, C104: CAPACITOR_0603_25V_1UF; 0603-CAP
C5, C6: CAPACITOR_0603_25V_47NF; 0603-CAP
C8, C13: CAPACITOR_0603_10V_68NF; 0603-CAP
C9: CAPACITOR_0603_10V_680PF; 0603-CAP
C10, C100, C103: CAPACITOR_0603_25V_0.1UF; 0603-CAP
C11: CAPACITOR_0603_10V_1UF; 0603-CAP
C12: CAPACITOR_0603_35V_1UF; 0603-CAP
C105: CAPACITOR_1206_25V_33UF; 1206-CAP
D1, D4, D5, D6: TVS_15V; SOT-23
D2, D3: SCHOTTKY_SOD323_30V; SOD-323
D7, D8, D9, D17: LED_0603_BLUE; 0603-LED
D10: LED_0603_ORANGE; 0603-LED
D11, D12: LED_0603_GREEN; 0603-LED
D13, D14: LED_0603_YELLOW; 0603-LED
D15, D16: LED_0603_RED; 0603-LED
J1, J3: CONNECTOR-4_SOURIAU_; SOURIAU_12-04
J2: CONNECTOR-3_8STA20435PN; SOURIAU_04-35
K1: RELAY_SOLIDSTATE_NO_CMX60D20; CRYDOM_CMX
Q1, Q2, Q3, Q4: TRANSISTOR_N_MOS_2-7K1S_TK100S04N1LLQ; DPAK(2-7K1S)
R1, R2, R3, R22: RESISTOR_0603_10K; 0603-RES
R4, R5: RESISTOR_SENSE__WSL40262L000FEB; 4026
R6, R8: RESISTOR_0805_0.62; 0805-RES
R7, R23: RESISTOR_0603_41.2K; 0603-RES
R9, R24: RESISTOR_0603_13K; 0603-RES
R10, R25: RESISTOR_0603_5.49K; 0603-RES
R11, R26: RESISTOR_0603_1.13M; 0603-RES
R12, R13, R14, R15, R16, R17, R18, R19, R20, R21: RESISTOR_0603_1K; 0603-RES
R100, R101: RESISTOR_0603_DNP; 0603-RES
TP1, TP2, TP3, TP4, TP5, TP6, TP7, TP8, TP9, TP10, TP11, TP12: TEST_POINT; 5015
U1: LTC4421; SSOP-36
XF1, XF2, XF3, XF4: FUSE_HOLDER_MINIBLADEPTH; 3568

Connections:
!CH1: D13.1 (C), U1.13 (!CH1)
!CH2: D14.1 (C), U1.24 (!CH2)
!FAULT1: D15.1 (C), U1.15 (!FAULT1)
!FAULT2: D16.1 (C), U1.22 (!FAULT2)
!SHDN: D2.C, D3.C, D10.1 (C), R3.2, TP11.1, U1.12 (!DISABLE1), U1.21 (!SHDN), U1.25 (!DISABLE2)
!VALID1: D11.1 (C), U1.14 (!VALID1)
!VALID2: D12.1 (C), U1.23 (!VALID2)
BATTERY: J1.1, J1.2, TP1.1, XF1.3 (2), XF1.4 (2), XF2.1, XF2.2 (1)
CONVIN: A1.1 (+VIN), C103.1, C104.1, C105.1, D1.3 (C), K1.2 (CONTACT2)
CONVOUT: A1.7 (+SENSE), A1.8 (+VOUT), C100.1, C101.1, C102.1, D5.3 (C), Q3.2 (D), R6.2, R11.2, R13.2, R100.2, TP8.1, U1.30 (V2)
CPO: C12.2, TP12.1, U1.1 (CPO)
DCDC_VICOR: J3.1, J3.2, TP4.1, XF4.1, XF4.2 (1)
DCDC_VICORPREMOS: D6.3 (C), Q4.2 (D), R8.2, R12.2, R26.2, U1.7 (V1), XF4.3 (2), XF4.4 (2)
GATE1: C6.2, Q1.1 (G), Q4.1 (G), TP9.1, U1.6 (GATE1)
GATE2: C5.2, Q2.1 (G), Q3.1 (G), TP2.1, U1.31 (GATE2)
GLVMS: D2.A, J2.B (2), R2.2
GND: A1.3 (-VIN), A1.4 (-VOUT), A1.5 (-SENSE), C1.P$2 (MINUS), C2.2, C3.2, C4.2, C7.2, C8.2, C9.2, C10.1, C11.2, C13.2, C100.2, C101.2, C102.2, C103.2, C104.2, C105.2, D1.1 (A), D4.1 (A), D5.1 (A), D6.1 (A), D7.1 (C), D8.1 (C), D9.1 (C), D17.1 (C), J2.A (1), K1.4 (CONTROL-), R1.1, R2.1, R3.1, R7.1, R23.1, R101.1, TP6.1, U1.20 (RETRY), U1.35 (GND)
INTVDD: C11.1, R14.2, R16.2, R17.2, R18.2, R19.2, R20.2, R21.2, TP3.1, U1.16 (CASIN), U1.17 (INTVDD)
unnamed: C9.1, U1.19 (QUAL)
unnamed: C13.1, U1.11 (TMR1)
unnamed: C8.1, U1.26 (TMR2)
unnamed: C4.1, R6.1
unnamed: D17.2 (A), R22.1
unnamed: D8.2 (A), R13.1
unnamed: D7.2 (A), R12.1
unnamed: D9.2 (A), R14.1
unnamed: D16.2 (A), R21.1
unnamed: K1.1 (CONTACT1), XF1.1, XF1.2 (1)
unnamed: D15.2 (A), R20.1
unnamed: D14.2 (A), R19.1
unnamed: A1.6 (TRIM), R100.1, R101.2
unnamed: D13.2 (A), R18.1
unnamed: R5.3, U1.33 (SENSE2)
unnamed: D12.2 (A), R17.1
unnamed: R5.4, U1.34 (OUT2)
unnamed: D11.2 (A), R16.1
unnamed: C7.1, R8.1
unnamed: R4.3, U1.4 (SENSE1)
unnamed: R24.2, R25.1, U1.9 (UVR1)
unnamed: R23.2, R24.1, U1.10 (OV1)
unnamed: R10.2, R11.1, U1.29 (UVF2)
unnamed: R9.2, R10.1, U1.28 (UVR2)
unnamed: R7.2, R9.1, U1.27 (OV2)
unnamed: D10.2 (A), R15.1
unnamed: Q2.2 (D), R5.1
unnamed: R4.4, U1.3 (OUT1)
unnamed: Q1.2 (D), R4.1
OUT: J1.3, J1.4, TP7.1, XF2.3 (2), XF2.4 (2), XF3.3 (2), XF3.4 (2)
OUTPREFUSE: C1.P$1 (PLUS), C2.1, C3.1, C10.2, C12.1, D4.3 (C), R4.2, R5.2, R22.2, U1.2 (CPOREF), U1.36 (EXTVDD), XF3.1, XF3.2 (1)
SHDNLINE: A1.2 (ON/OFF), K1.3 (CONTROL+), R15.2
SOURCE1: C6.1, Q1.3 (S), Q4.3 (S), TP10.1, U1.5 (SOURCE1)
SOURCE2: C5.1, Q2.3 (S), Q3.3 (S), TP5.1, U1.32 (SOURCE2)
START: D3.A, J2.C (3), R1.2
UVF1: R25.2, R26.1, U1.8 (UVF1)

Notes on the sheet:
DCDC_VICOR: OV Rising: 14.44V OV Falling: 12.34V UV Rising: 10.98V UV Falling: 9.97V CONVOUT: OV Rising: 14.44V OV Falling: 12.34V UV Rising: 10.98V UV Falling: 9.97V
tValid = 10.88ms
tTMR,FLT = 5.644ms
ILim = 12.5A
VALID1: DCDC_VICOR is within OV/UV for time tValid VALID2: CONVOUT is within OV/UV for time tValid CH1: DCDC_VICOR is the output CH2: CONVOUT is the output FAULT1: Current limit fault on DCDC_VICOR FAULT2: Current limit fault on CONVOUT

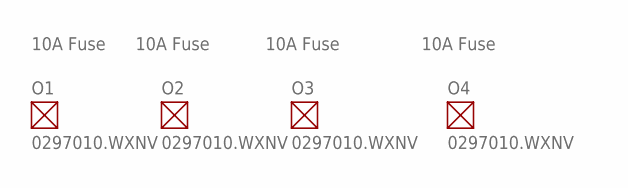
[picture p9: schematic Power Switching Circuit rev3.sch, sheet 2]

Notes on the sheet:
10A Fuse

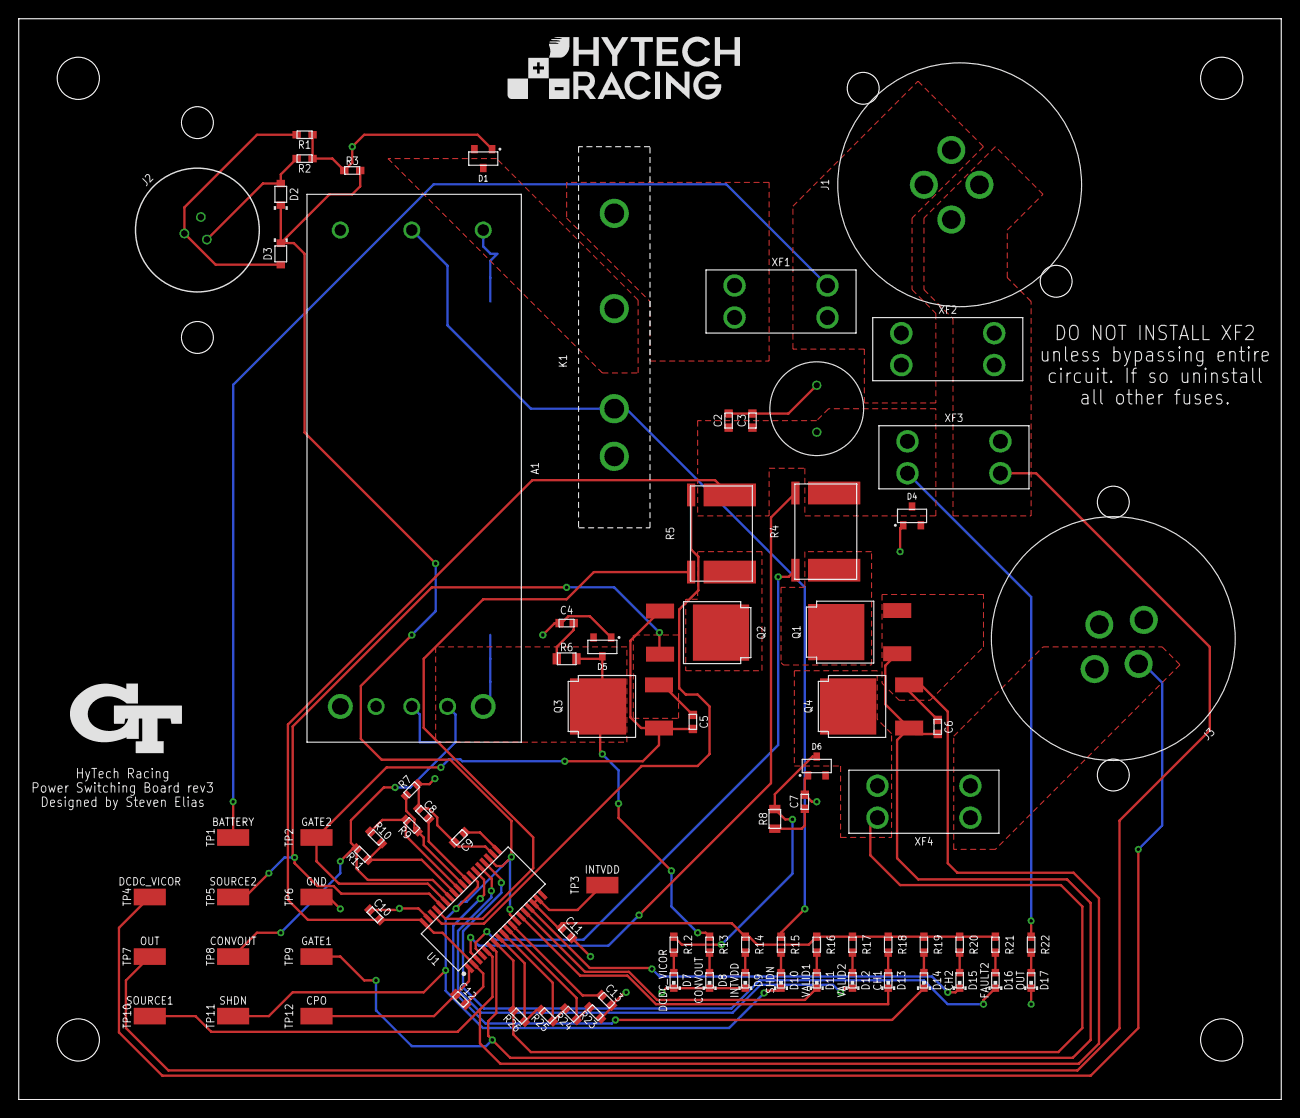
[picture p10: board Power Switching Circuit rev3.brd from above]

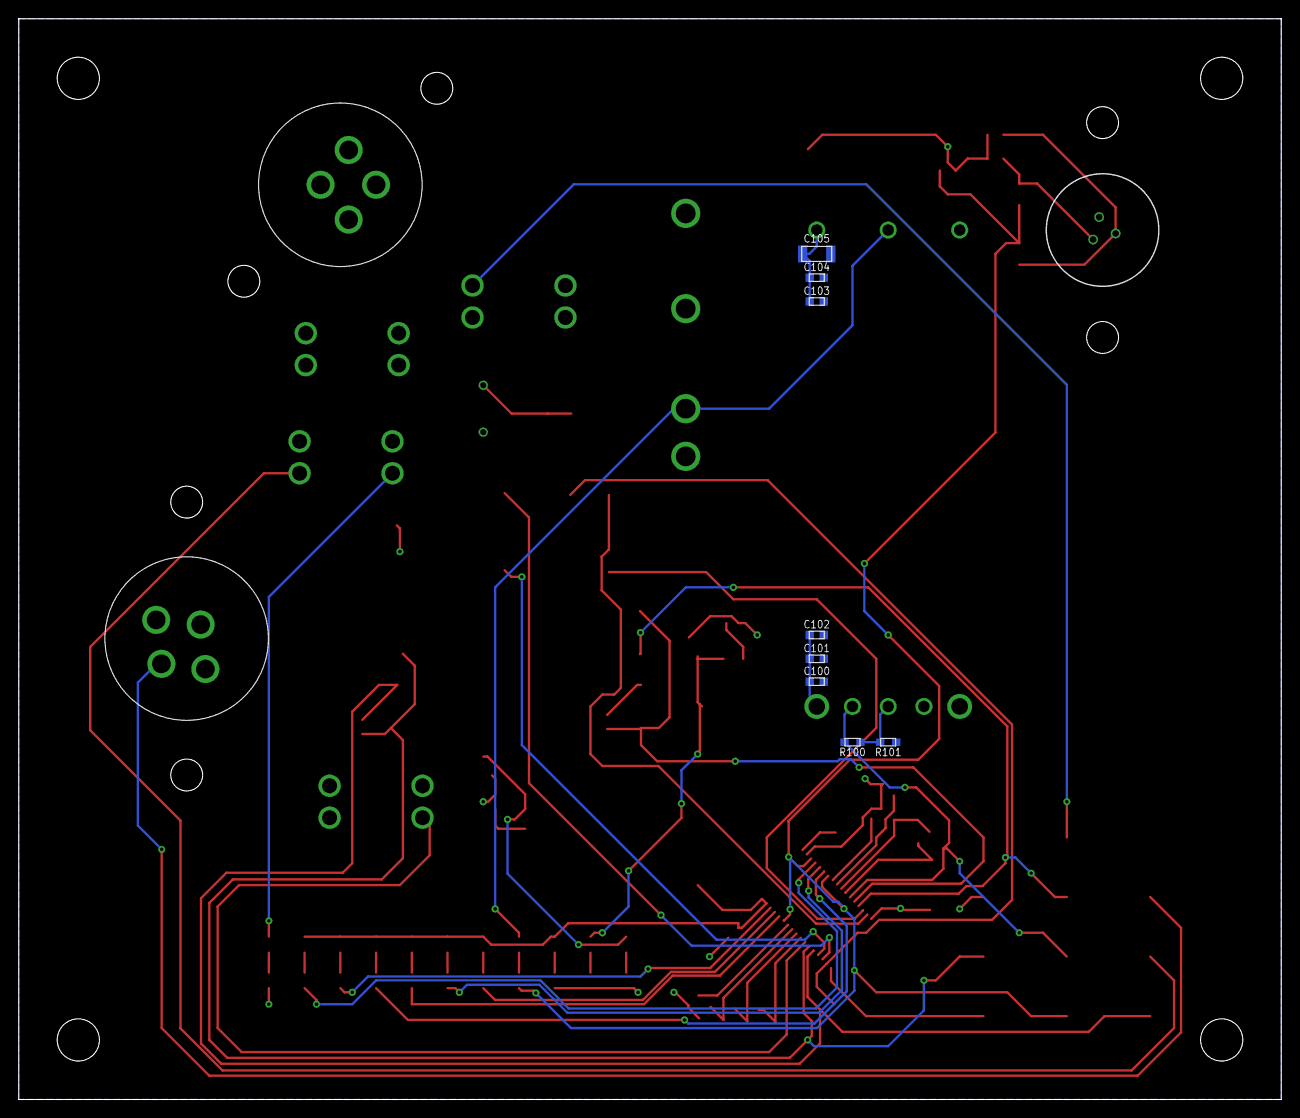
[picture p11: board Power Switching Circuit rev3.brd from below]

Board: 2 copper layers, 134.6 x 115.2 mm, 96 parts (8 on the bottom side), 54 nets.

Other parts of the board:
U$1, U$2, U$5, U$6: MOUNTING_M4
U$3: LOGO_HYTECH_MEDIUM
U$4: LOGO_GT_MEDIUM

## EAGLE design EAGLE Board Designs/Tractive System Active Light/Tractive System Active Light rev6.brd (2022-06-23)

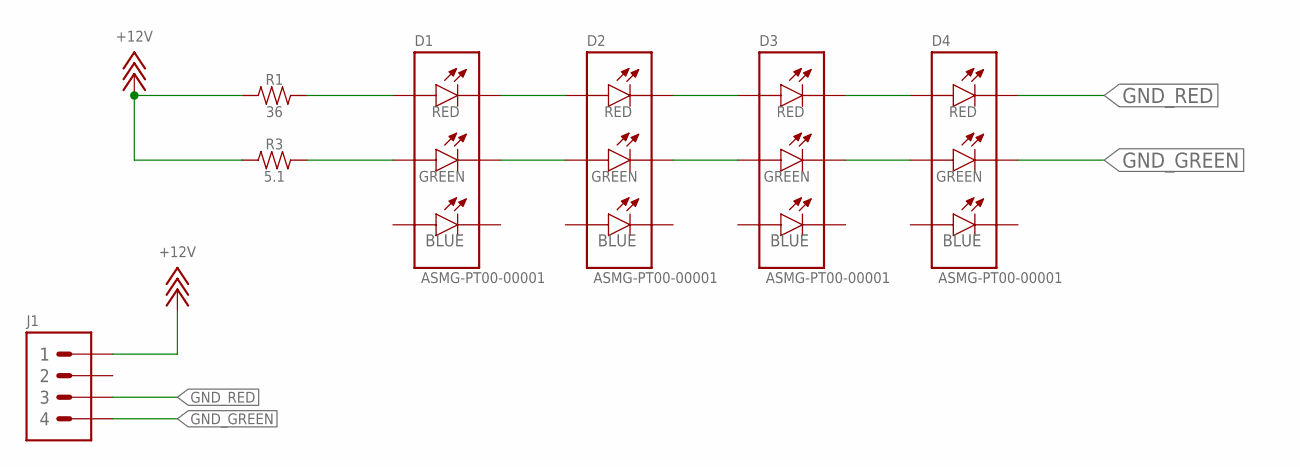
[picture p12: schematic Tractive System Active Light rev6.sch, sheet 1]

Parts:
D1, D2, D3, D4: LED_RGB_ASMG-PT00-00001; ASMG-PT00-00001
J1: CONNECTOR-4_μF_S_RA_; MOLEX_MICROFIT_SMD_RIGHTANGLE_04_DUAL
R1: RESISTOR_0805_36; 0805-RES
R3: RESISTOR_0805_5.1; 0805-RES

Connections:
+12V: J1.1, R1.1, R3.1
GND_GREEN: D4.2 (GREEN-), J1.4
GND_RED: D4.1 (RED-), J1.3
unnamed: D3.1 (RED-), D4.4 (RED+), D4.THERMAL (RED+)
unnamed: D3.2 (GREEN-), D4.5 (GREEN+)
unnamed: D2.1 (RED-), D3.4 (RED+), D3.THERMAL (RED+)
unnamed: D2.2 (GREEN-), D3.5 (GREEN+)
unnamed: D1.1 (RED-), D2.4 (RED+), D2.THERMAL (RED+)
unnamed: D1.2 (GREEN-), D2.5 (GREEN+)
unnamed: D1.4 (RED+), D1.THERMAL (RED+), R1.2
unnamed: D1.5 (GREEN+), R3.2

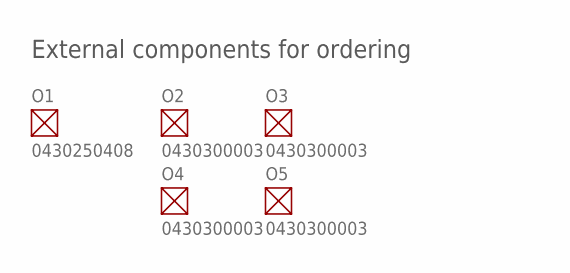
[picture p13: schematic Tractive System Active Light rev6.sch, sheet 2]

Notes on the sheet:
External components for ordering

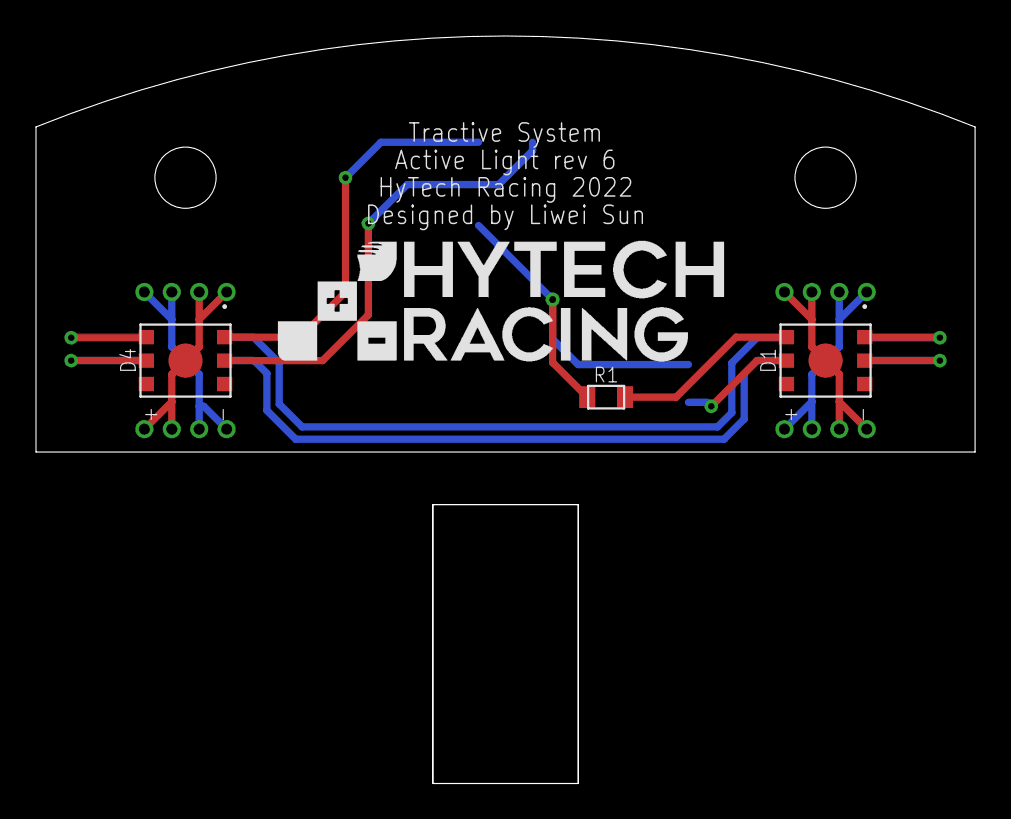
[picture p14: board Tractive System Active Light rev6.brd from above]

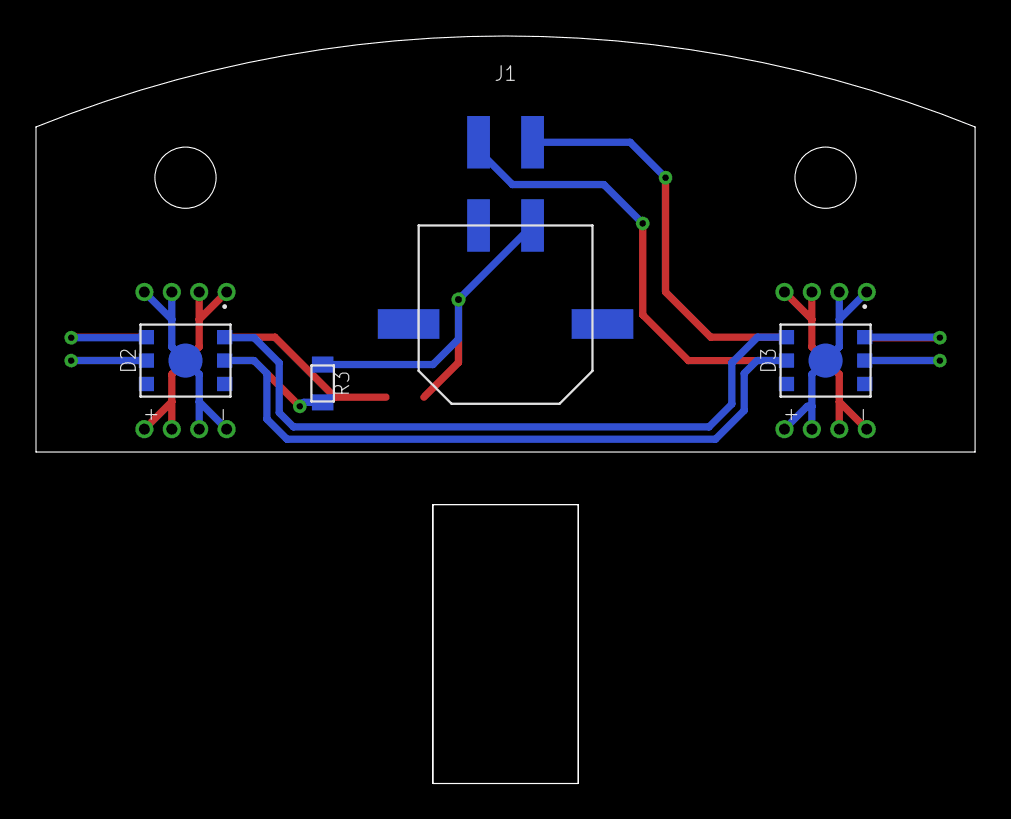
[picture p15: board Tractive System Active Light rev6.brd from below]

Board: 2 copper layers, 52.2 x 41.5 mm, 10 parts (4 on the bottom side), 11 nets.

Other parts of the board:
U$1, U$3: MOUNTING_M3
U$2: LOGO_HYTECH_MEDIUM

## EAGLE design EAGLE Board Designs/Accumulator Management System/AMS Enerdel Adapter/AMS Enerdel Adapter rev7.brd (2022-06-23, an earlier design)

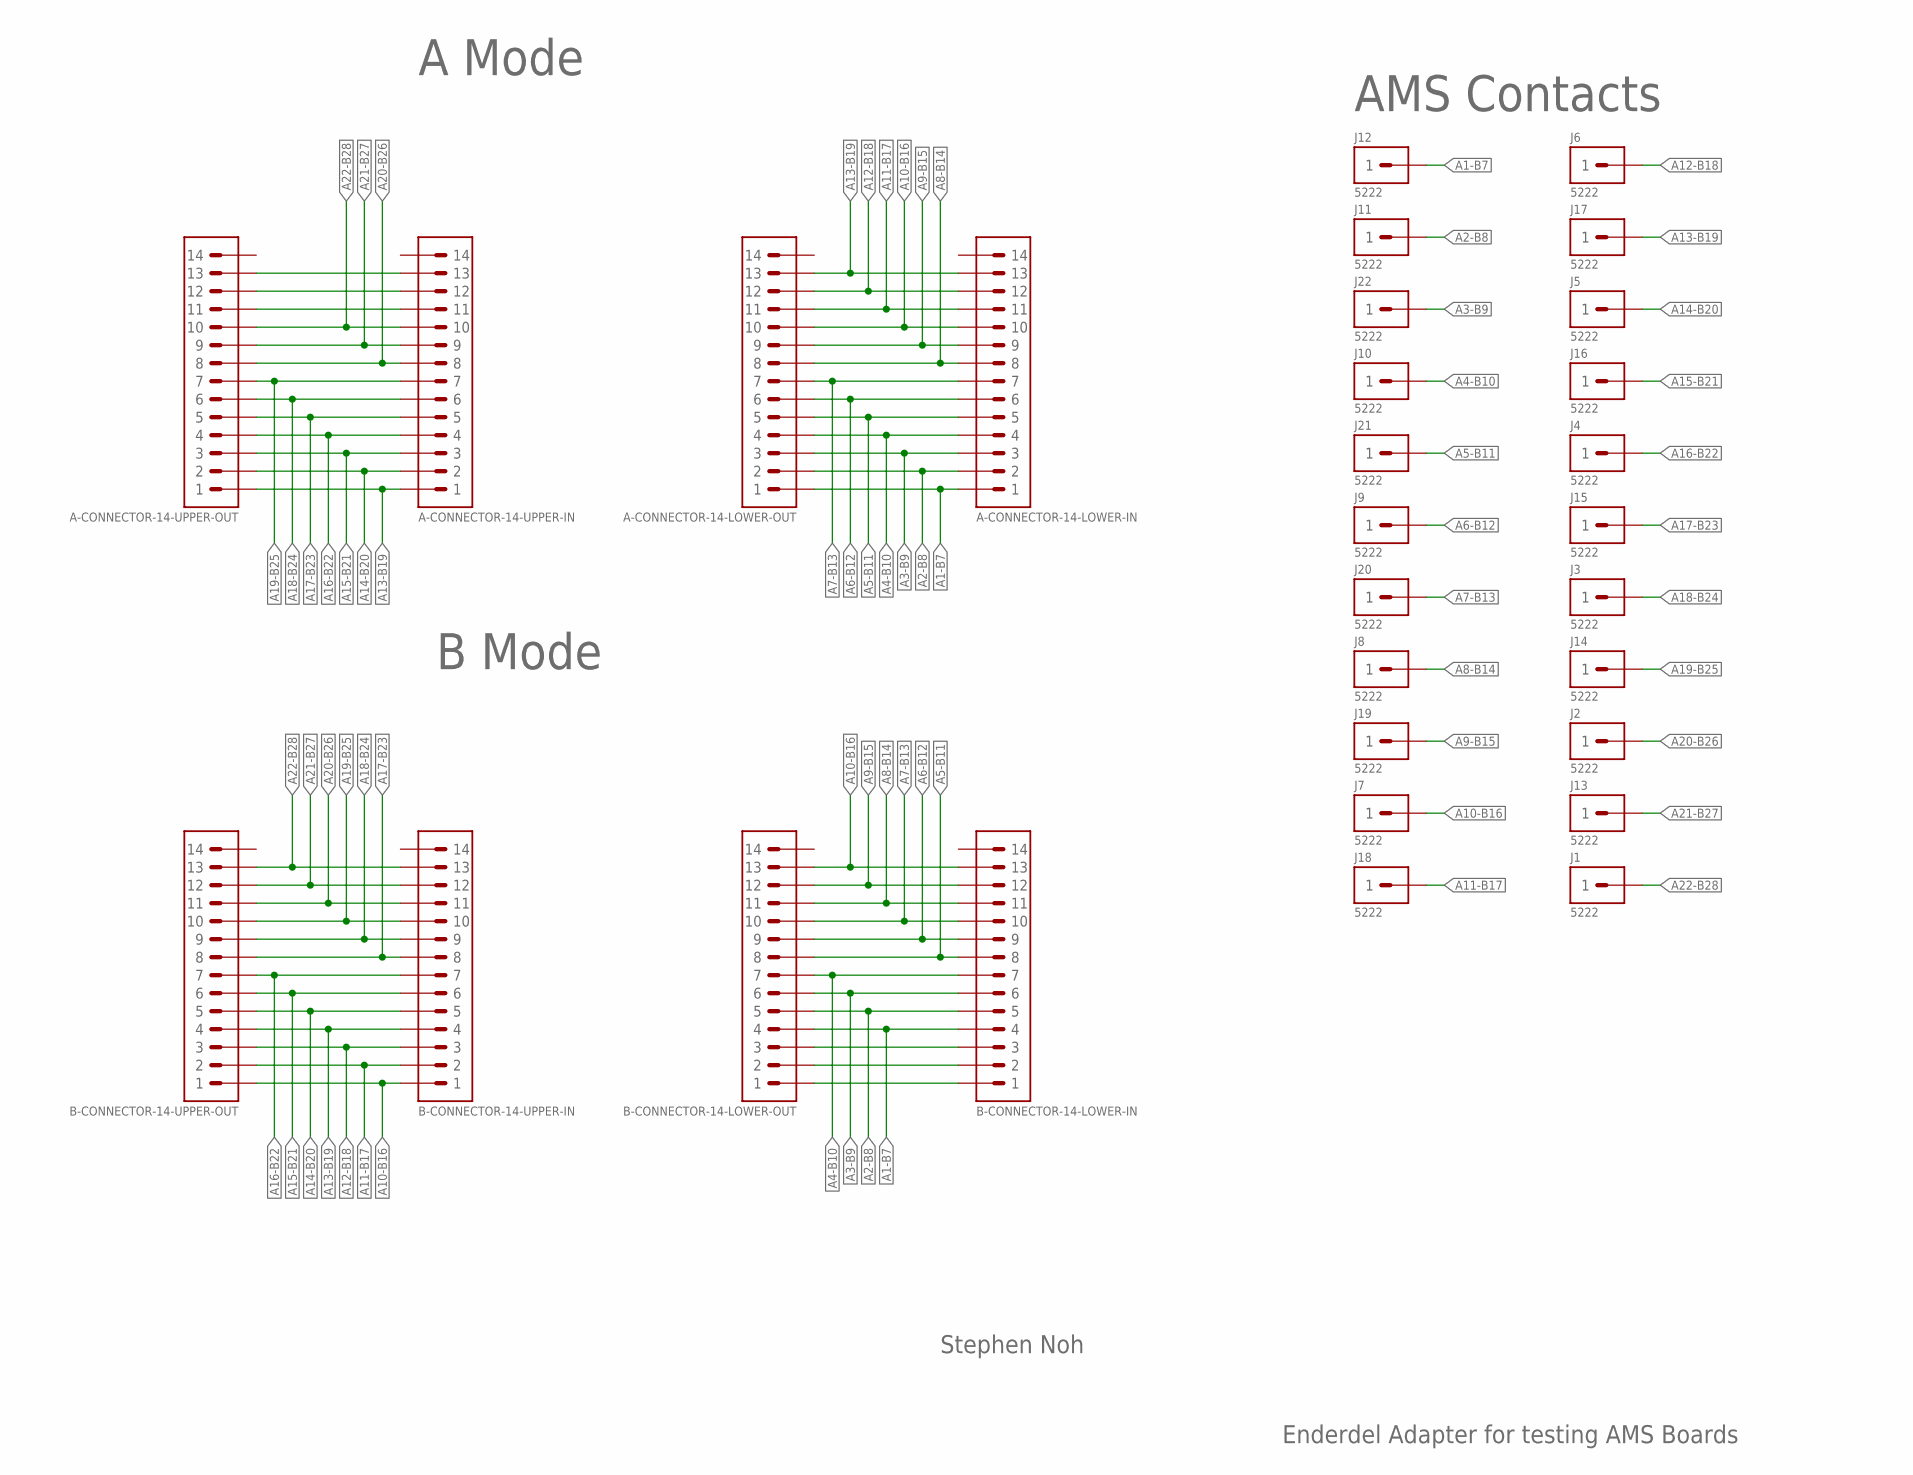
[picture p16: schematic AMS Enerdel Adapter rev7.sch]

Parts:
A-CONNECTOR-14-LOWER-IN, A-CONNECTOR-14-LOWER-OUT: CONNECTOR-14_MINIFIT_; MOLEX_MINIFIT_PTH_14
A-CONNECTOR-14-UPPER-IN, A-CONNECTOR-14-UPPER-OUT: CONNECTOR-14_NANOFIT_; MOLEX_NANOFIT_PTH_14
B-CONNECTOR-14-LOWER-IN, B-CONNECTOR-14-LOWER-OUT: CONNECTOR-14_MINIFIT_; MOLEX_MINIFIT_PTH_14
B-CONNECTOR-14-UPPER-IN, B-CONNECTOR-14-UPPER-OUT: CONNECTOR-14_NANOFIT_; MOLEX_NANOFIT_PTH_14
J1, J2, J3, J4, J5, J6, J7, J8, J9, J10, J11, J12, J13, J14, J15, J16, J17, J18, J19, J20, J21, J22: CONNECTOR-1_5222_; 5222

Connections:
A1-B7: A-CONNECTOR-14-LOWER-IN.1, A-CONNECTOR-14-LOWER-OUT.1, B-CONNECTOR-14-LOWER-IN.4, B-CONNECTOR-14-LOWER-OUT.4, J12.1
A2-B8: A-CONNECTOR-14-LOWER-IN.2, A-CONNECTOR-14-LOWER-OUT.2, B-CONNECTOR-14-LOWER-IN.5, B-CONNECTOR-14-LOWER-OUT.5, J11.1
A3-B9: A-CONNECTOR-14-LOWER-IN.3, A-CONNECTOR-14-LOWER-OUT.3, B-CONNECTOR-14-LOWER-IN.6, B-CONNECTOR-14-LOWER-OUT.6, J22.1
A4-B10: A-CONNECTOR-14-LOWER-IN.4, A-CONNECTOR-14-LOWER-OUT.4, B-CONNECTOR-14-LOWER-IN.7, B-CONNECTOR-14-LOWER-OUT.7, J10.1
A5-B11: A-CONNECTOR-14-LOWER-IN.5, A-CONNECTOR-14-LOWER-OUT.5, B-CONNECTOR-14-LOWER-IN.8, B-CONNECTOR-14-LOWER-OUT.8, J21.1
A6-B12: A-CONNECTOR-14-LOWER-IN.6, A-CONNECTOR-14-LOWER-OUT.6, B-CONNECTOR-14-LOWER-IN.9, B-CONNECTOR-14-LOWER-OUT.9, J9.1
A7-B13: A-CONNECTOR-14-LOWER-IN.7, A-CONNECTOR-14-LOWER-OUT.7, B-CONNECTOR-14-LOWER-IN.10, B-CONNECTOR-14-LOWER-OUT.10, J20.1
A8-B14: A-CONNECTOR-14-LOWER-IN.8, A-CONNECTOR-14-LOWER-OUT.8, B-CONNECTOR-14-LOWER-IN.11, B-CONNECTOR-14-LOWER-OUT.11, J8.1
A9-B15: A-CONNECTOR-14-LOWER-IN.9, A-CONNECTOR-14-LOWER-OUT.9, B-CONNECTOR-14-LOWER-IN.12, B-CONNECTOR-14-LOWER-OUT.12, J19.1
A10-B16: A-CONNECTOR-14-LOWER-IN.10, A-CONNECTOR-14-LOWER-OUT.10, B-CONNECTOR-14-LOWER-IN.13, B-CONNECTOR-14-LOWER-OUT.13, B-CONNECTOR-14-UPPER-IN.1, B-CONNECTOR-14-UPPER-OUT.1, J7.1
A11-B17: A-CONNECTOR-14-LOWER-IN.11, A-CONNECTOR-14-LOWER-OUT.11, B-CONNECTOR-14-UPPER-IN.2, B-CONNECTOR-14-UPPER-OUT.2, J18.1
A12-B18: A-CONNECTOR-14-LOWER-IN.12, A-CONNECTOR-14-LOWER-OUT.12, B-CONNECTOR-14-UPPER-IN.3, B-CONNECTOR-14-UPPER-OUT.3, J6.1
A13-B19: A-CONNECTOR-14-LOWER-IN.13, A-CONNECTOR-14-LOWER-OUT.13, A-CONNECTOR-14-UPPER-IN.1, A-CONNECTOR-14-UPPER-OUT.1, B-CONNECTOR-14-UPPER-IN.4, B-CONNECTOR-14-UPPER-OUT.4, J17.1
A14-B20: A-CONNECTOR-14-UPPER-IN.2, A-CONNECTOR-14-UPPER-OUT.2, B-CONNECTOR-14-UPPER-IN.5, B-CONNECTOR-14-UPPER-OUT.5, J5.1
A15-B21: A-CONNECTOR-14-UPPER-IN.3, A-CONNECTOR-14-UPPER-OUT.3, B-CONNECTOR-14-UPPER-IN.6, B-CONNECTOR-14-UPPER-OUT.6, J16.1
A16-B22: A-CONNECTOR-14-UPPER-IN.4, A-CONNECTOR-14-UPPER-OUT.4, B-CONNECTOR-14-UPPER-IN.7, B-CONNECTOR-14-UPPER-OUT.7, J4.1
A17-B23: A-CONNECTOR-14-UPPER-IN.5, A-CONNECTOR-14-UPPER-OUT.5, B-CONNECTOR-14-UPPER-IN.8, B-CONNECTOR-14-UPPER-OUT.8, J15.1
A18-B24: A-CONNECTOR-14-UPPER-IN.6, A-CONNECTOR-14-UPPER-OUT.6, B-CONNECTOR-14-UPPER-IN.9, B-CONNECTOR-14-UPPER-OUT.9, J3.1
A19-B25: A-CONNECTOR-14-UPPER-IN.7, A-CONNECTOR-14-UPPER-OUT.7, B-CONNECTOR-14-UPPER-IN.10, B-CONNECTOR-14-UPPER-OUT.10, J14.1
A20-B26: A-CONNECTOR-14-UPPER-IN.8, A-CONNECTOR-14-UPPER-OUT.8, B-CONNECTOR-14-UPPER-IN.11, B-CONNECTOR-14-UPPER-OUT.11, J2.1
A21-B27: A-CONNECTOR-14-UPPER-IN.9, A-CONNECTOR-14-UPPER-OUT.9, B-CONNECTOR-14-UPPER-IN.12, B-CONNECTOR-14-UPPER-OUT.12, J13.1
A22-B28: A-CONNECTOR-14-UPPER-IN.10, A-CONNECTOR-14-UPPER-OUT.10, B-CONNECTOR-14-UPPER-IN.13, B-CONNECTOR-14-UPPER-OUT.13, J1.1
B-PASS1: B-CONNECTOR-14-LOWER-IN.3, B-CONNECTOR-14-LOWER-OUT.3
B-PASS2: B-CONNECTOR-14-LOWER-IN.2, B-CONNECTOR-14-LOWER-OUT.2
B-PASS3: B-CONNECTOR-14-LOWER-IN.1, B-CONNECTOR-14-LOWER-OUT.1
unnamed: A-CONNECTOR-14-UPPER-IN.11, A-CONNECTOR-14-UPPER-OUT.11
unnamed: A-CONNECTOR-14-UPPER-IN.12, A-CONNECTOR-14-UPPER-OUT.12
unnamed: A-CONNECTOR-14-UPPER-IN.13, A-CONNECTOR-14-UPPER-OUT.13

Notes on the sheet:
Stephen Noh
AMS Contacts
A Mode
Enderdel Adapter for testing AMS Boards
B Mode

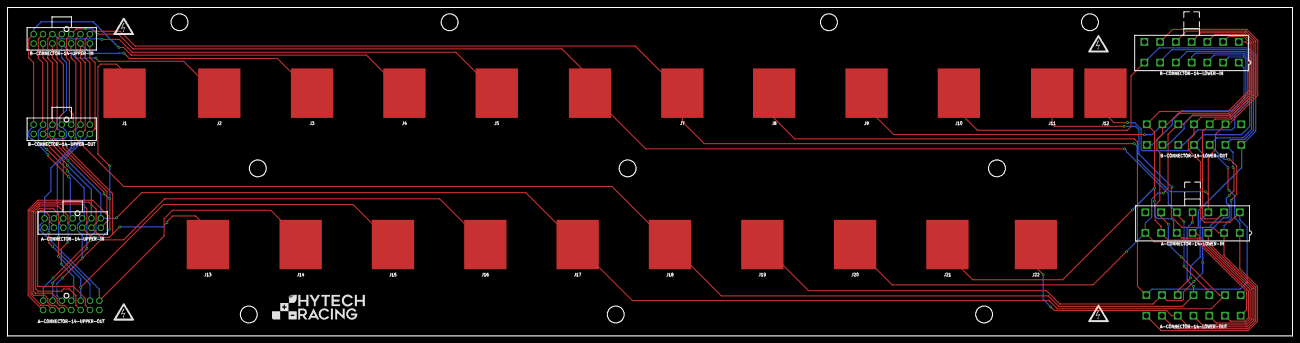
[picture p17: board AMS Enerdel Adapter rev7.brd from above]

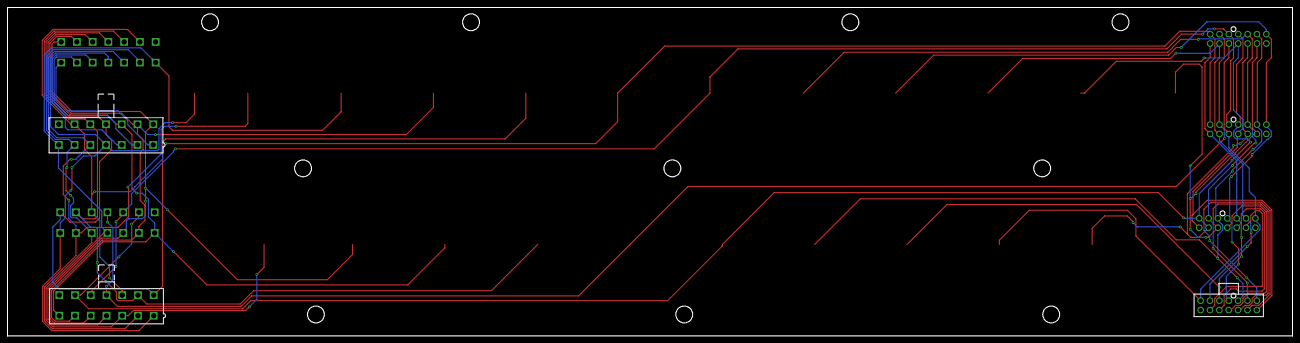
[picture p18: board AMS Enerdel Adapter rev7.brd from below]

Board: 2 copper layers, 342.9 x 87.6 mm, 35 parts (3 on the bottom side), 28 nets.

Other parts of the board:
U$1, U$2, U$3, U$4: HV_0.50"
U$5: LOGO_HYTECH_1.0"

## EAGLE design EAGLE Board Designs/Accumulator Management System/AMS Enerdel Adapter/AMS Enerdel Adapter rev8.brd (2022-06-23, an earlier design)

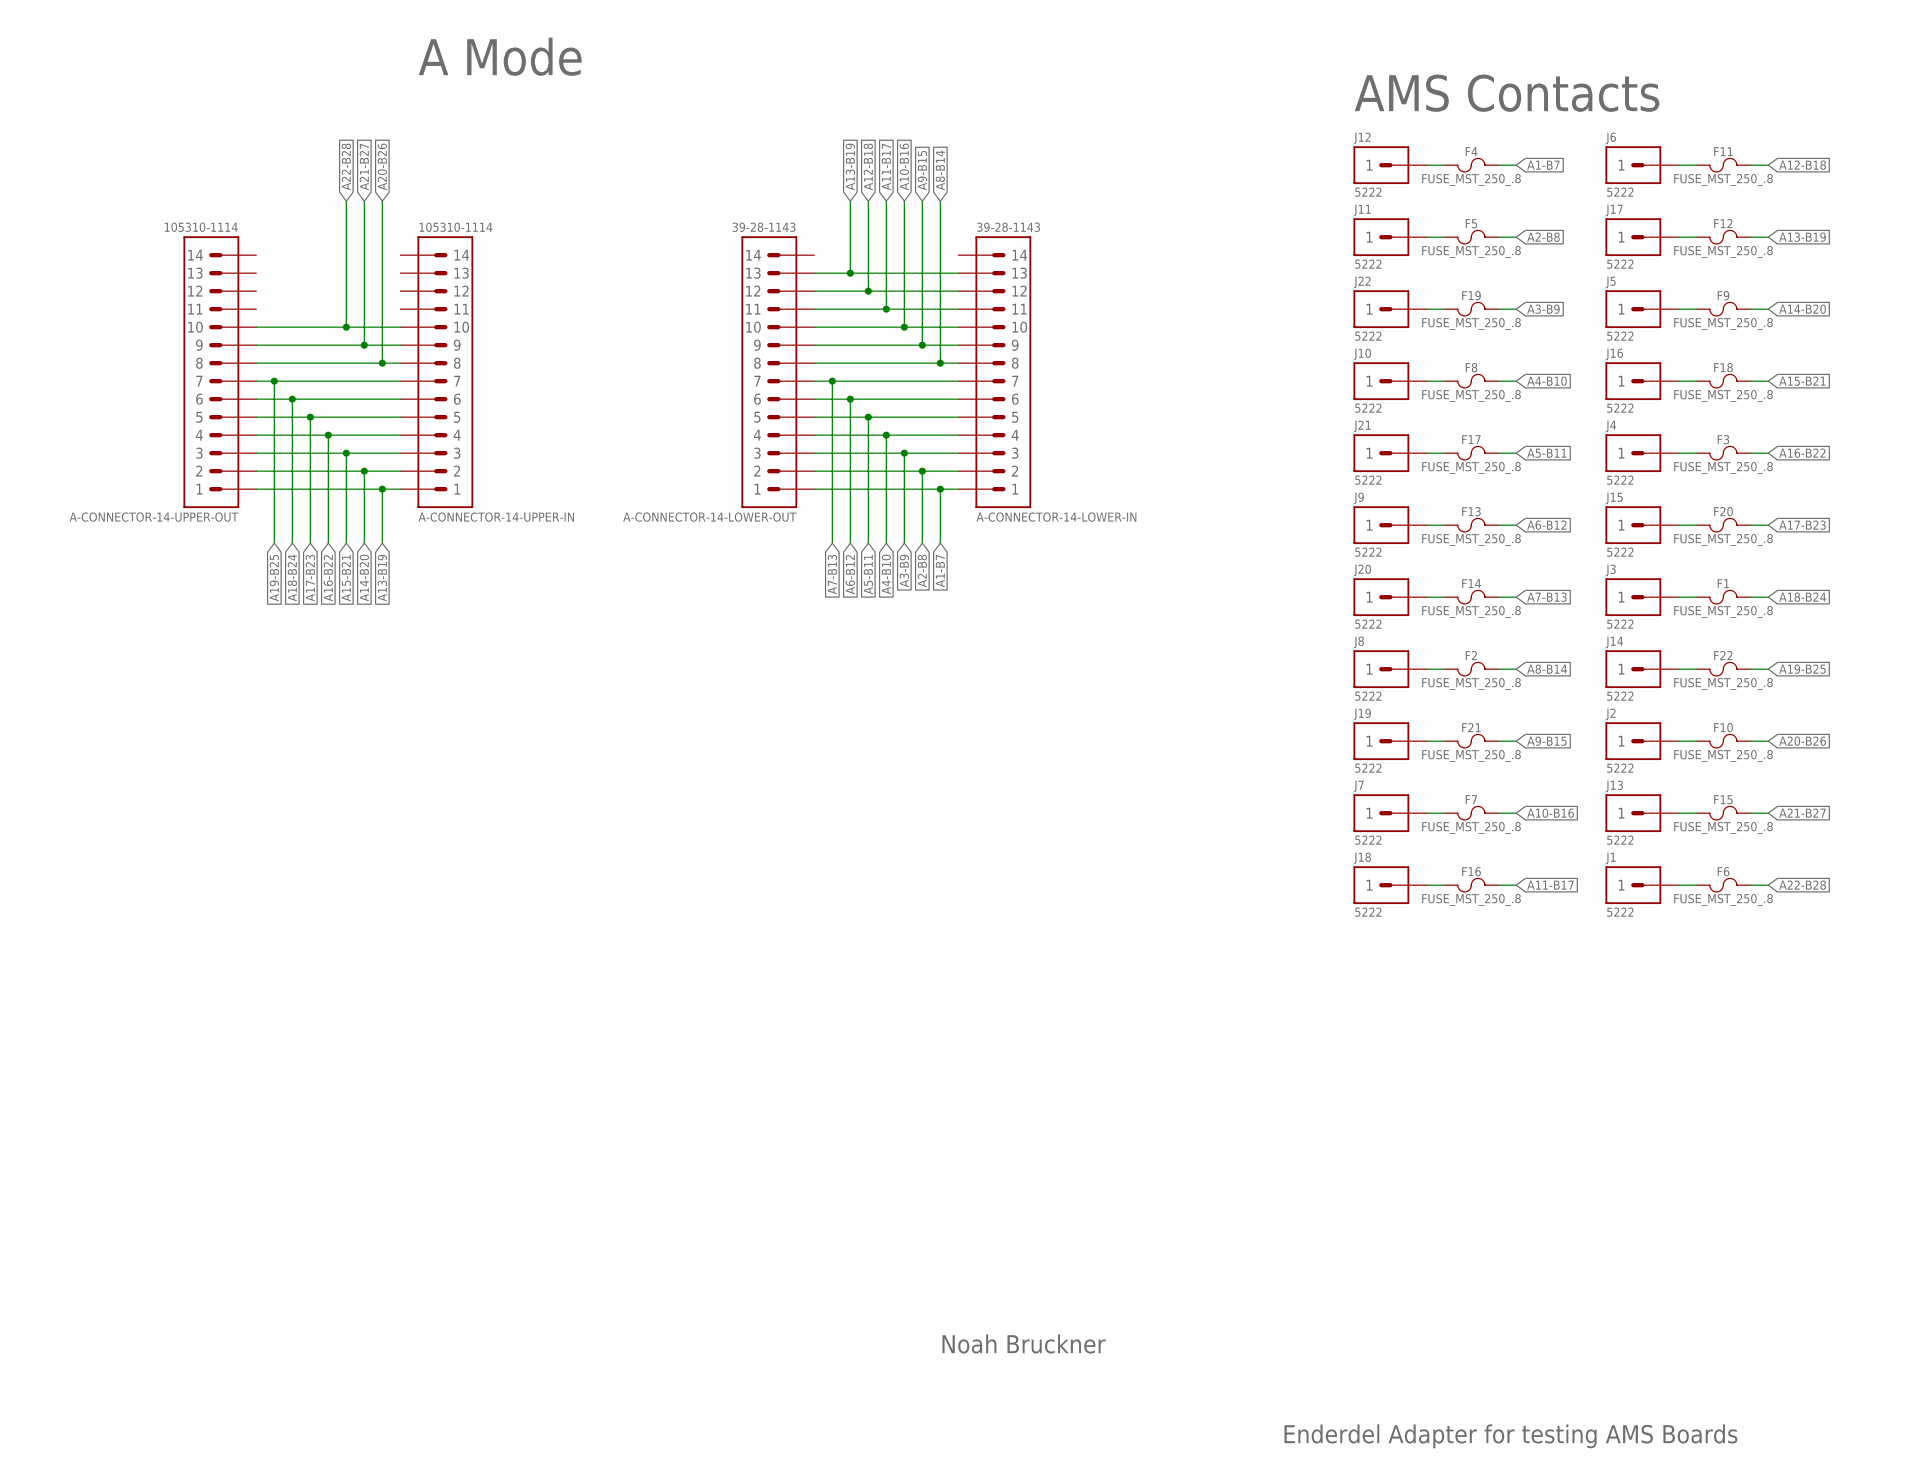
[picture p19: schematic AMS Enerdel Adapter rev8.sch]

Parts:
A-CONNECTOR-14-LOWER-IN, A-CONNECTOR-14-LOWER-OUT: CONNECTOR-14_MINIFIT_; MOLEX_MINIFIT_PTH_14; MPN 39-28-1143
A-CONNECTOR-14-UPPER-IN, A-CONNECTOR-14-UPPER-OUT: CONNECTOR-14_NANOFIT_; MOLEX_NANOFIT_PTH_14; MPN 105310-1114
F1, F2, F3, F4, F5, F6, F7, F8, F9, F10, F11, F12, F13, F14, F15, F16, F17, F18, F19, F20, F21, F22: FUSE_MST_250_.8; MST_250
J1, J2, J3, J4, J5, J6, J7, J8, J9, J10, J11, J12, J13, J14, J15, J16, J17, J18, J19, J20, J21, J22: CONNECTOR-1_5222_; 5222

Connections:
A1-B7: A-CONNECTOR-14-LOWER-IN.1, A-CONNECTOR-14-LOWER-OUT.1, F4.2
A2-B8: A-CONNECTOR-14-LOWER-IN.2, A-CONNECTOR-14-LOWER-OUT.2, F5.2
A3-B9: A-CONNECTOR-14-LOWER-IN.3, A-CONNECTOR-14-LOWER-OUT.3, F19.2
A4-B10: A-CONNECTOR-14-LOWER-IN.4, A-CONNECTOR-14-LOWER-OUT.4, F8.2
A5-B11: A-CONNECTOR-14-LOWER-IN.5, A-CONNECTOR-14-LOWER-OUT.5, F17.2
A6-B12: A-CONNECTOR-14-LOWER-IN.6, A-CONNECTOR-14-LOWER-OUT.6, F13.2
A7-B13: A-CONNECTOR-14-LOWER-IN.7, A-CONNECTOR-14-LOWER-OUT.7, F14.2
A8-B14: A-CONNECTOR-14-LOWER-IN.8, A-CONNECTOR-14-LOWER-OUT.8, F2.2
A9-B15: A-CONNECTOR-14-LOWER-IN.9, A-CONNECTOR-14-LOWER-OUT.9, F21.2
A10-B16: A-CONNECTOR-14-LOWER-IN.10, A-CONNECTOR-14-LOWER-OUT.10, F7.2
A11-B17: A-CONNECTOR-14-LOWER-IN.11, A-CONNECTOR-14-LOWER-OUT.11, F16.2
A12-B18: A-CONNECTOR-14-LOWER-IN.12, A-CONNECTOR-14-LOWER-OUT.12, F11.2
A13-B19: A-CONNECTOR-14-LOWER-IN.13, A-CONNECTOR-14-LOWER-OUT.13, A-CONNECTOR-14-UPPER-IN.1, A-CONNECTOR-14-UPPER-OUT.1, F12.2
A14-B20: A-CONNECTOR-14-UPPER-IN.2, A-CONNECTOR-14-UPPER-OUT.2, F9.2
A15-B21: A-CONNECTOR-14-UPPER-IN.3, A-CONNECTOR-14-UPPER-OUT.3, F18.2
A16-B22: A-CONNECTOR-14-UPPER-IN.4, A-CONNECTOR-14-UPPER-OUT.4, F3.2
A17-B23: A-CONNECTOR-14-UPPER-IN.5, A-CONNECTOR-14-UPPER-OUT.5, F20.2
A18-B24: A-CONNECTOR-14-UPPER-IN.6, A-CONNECTOR-14-UPPER-OUT.6, F1.2
A19-B25: A-CONNECTOR-14-UPPER-IN.7, A-CONNECTOR-14-UPPER-OUT.7, F22.2
A20-B26: A-CONNECTOR-14-UPPER-IN.8, A-CONNECTOR-14-UPPER-OUT.8, F10.2
A21-B27: A-CONNECTOR-14-UPPER-IN.9, A-CONNECTOR-14-UPPER-OUT.9, F15.2
A22-B28: A-CONNECTOR-14-UPPER-IN.10, A-CONNECTOR-14-UPPER-OUT.10, F6.2
unnamed: F4.1, J12.1
unnamed: F5.1, J11.1
unnamed: F19.1, J22.1
unnamed: F8.1, J10.1
unnamed: F17.1, J21.1
unnamed: F13.1, J9.1
unnamed: F14.1, J20.1
unnamed: F2.1, J8.1
unnamed: F21.1, J19.1
unnamed: F7.1, J7.1
unnamed: F16.1, J18.1
unnamed: F6.1, J1.1
unnamed: F15.1, J13.1
unnamed: F10.1, J2.1
unnamed: F22.1, J14.1
unnamed: F1.1, J3.1
unnamed: F20.1, J15.1
unnamed: F3.1, J4.1
unnamed: F18.1, J16.1
unnamed: F9.1, J5.1
unnamed: F11.1, J6.1
unnamed: F12.1, J17.1

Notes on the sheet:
Noah Bruckner
AMS Contacts
A Mode
Enderdel Adapter for testing AMS Boards

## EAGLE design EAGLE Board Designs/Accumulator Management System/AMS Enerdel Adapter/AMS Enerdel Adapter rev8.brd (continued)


Board: 2 copper layers, 429.8 x 87.7 mm, 80 parts (0 on the bottom side), 44 nets.

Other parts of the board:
U$1, U$2, U$3, U$4, U$20, U$21, U$22, U$29, U$30, U$31: MOUNTING_M3
U$5, U$6, U$7, U$8, U$9, U$10, U$11, U$12, U$13, U$14, U$15, U$16, U$17, U$18, U$19, U$23, U$24, U$25, U$26, U$27, U$28: HV_LARGE
U$32: LOGO_HYTECH_1.0"

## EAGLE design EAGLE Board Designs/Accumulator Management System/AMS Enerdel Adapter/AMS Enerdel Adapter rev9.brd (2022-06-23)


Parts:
A-CONNECTOR-14-LOWER-IN, A-CONNECTOR-14-LOWER-OUT: CONNECTOR-14_MINIFIT_; MOLEX_MINIFIT_PTH_14; MPN 39-28-1143
A-CONNECTOR-14-UPPER-IN, A-CONNECTOR-14-UPPER-OUT: CONNECTOR-14_NANOFIT_; MOLEX_NANOFIT_PTH_14; MPN 105310-1114
F1, F2, F3, F4, F5, F6, F7, F8, F9, F10, F11, F12, F13, F14, F15, F16, F17, F18, F19, F20, F21, F22: FUSE_OMF_125_.63A; OMF_125
J1, J2, J3, J4, J5, J6, J7, J8, J9, J10, J11, J12, J13, J14, J15, J16, J17, J18, J19, J20, J21, J22: CONNECTOR-1_5222; 5222

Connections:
A1-B7: A-CONNECTOR-14-LOWER-IN.1, A-CONNECTOR-14-LOWER-OUT.1, F1.2
A2-B8: A-CONNECTOR-14-LOWER-IN.2, A-CONNECTOR-14-LOWER-OUT.2, F2.2
A3-B9: A-CONNECTOR-14-LOWER-IN.3, A-CONNECTOR-14-LOWER-OUT.3, F3.2
A4-B10: A-CONNECTOR-14-LOWER-IN.4, A-CONNECTOR-14-LOWER-OUT.4, F4.2
A5-B11: A-CONNECTOR-14-LOWER-IN.5, A-CONNECTOR-14-LOWER-OUT.5, F5.2
A6-B12: A-CONNECTOR-14-LOWER-IN.6, A-CONNECTOR-14-LOWER-OUT.6, F6.2
A7-B13: A-CONNECTOR-14-LOWER-IN.7, A-CONNECTOR-14-LOWER-OUT.7, F7.2
A8-B14: A-CONNECTOR-14-LOWER-IN.8, A-CONNECTOR-14-LOWER-OUT.8, F8.2
A9-B15: A-CONNECTOR-14-LOWER-IN.9, A-CONNECTOR-14-LOWER-OUT.9, F9.2
A10-B16: A-CONNECTOR-14-LOWER-IN.10, A-CONNECTOR-14-LOWER-OUT.10, F10.2
A11-B17: A-CONNECTOR-14-LOWER-IN.11, A-CONNECTOR-14-LOWER-OUT.11, F11.2
A12-B18: A-CONNECTOR-14-LOWER-IN.12, A-CONNECTOR-14-LOWER-OUT.12, F12.2
A13-B19: A-CONNECTOR-14-LOWER-IN.13, A-CONNECTOR-14-LOWER-OUT.13, A-CONNECTOR-14-UPPER-IN.1, A-CONNECTOR-14-UPPER-OUT.1, F13.1
A14-B20: A-CONNECTOR-14-UPPER-IN.2, A-CONNECTOR-14-UPPER-OUT.2, F14.1
A15-B21: A-CONNECTOR-14-UPPER-IN.3, A-CONNECTOR-14-UPPER-OUT.3, F15.1
A16-B22: A-CONNECTOR-14-UPPER-IN.4, A-CONNECTOR-14-UPPER-OUT.4, F16.1
A17-B23: A-CONNECTOR-14-UPPER-IN.5, A-CONNECTOR-14-UPPER-OUT.5, F17.1
A18-B24: A-CONNECTOR-14-UPPER-IN.6, A-CONNECTOR-14-UPPER-OUT.6, F18.1
A19-B25: A-CONNECTOR-14-UPPER-IN.7, A-CONNECTOR-14-UPPER-OUT.7, F19.1
A20-B26: A-CONNECTOR-14-UPPER-IN.8, A-CONNECTOR-14-UPPER-OUT.8, F20.1
A21-B27: A-CONNECTOR-14-UPPER-IN.9, A-CONNECTOR-14-UPPER-OUT.9, F21.1
A22-B28: A-CONNECTOR-14-UPPER-IN.10, A-CONNECTOR-14-UPPER-OUT.10, F22.1
unnamed: F1.1, J12.1
unnamed: F2.1, J11.1
unnamed: F3.1, J22.1
unnamed: F4.1, J10.1
unnamed: F5.1, J21.1
unnamed: F6.1, J9.1
unnamed: F7.1, J20.1
unnamed: F8.1, J8.1
unnamed: F9.1, J19.1
unnamed: F10.1, J7.1
unnamed: F11.1, J18.1
unnamed: F22.2, J1.1
unnamed: F21.2, J13.1
unnamed: F20.2, J2.1
unnamed: F19.2, J14.1
unnamed: F18.2, J3.1
unnamed: F17.2, J15.1
unnamed: F16.2, J4.1
unnamed: F15.2, J16.1
unnamed: F14.2, J5.1
unnamed: F12.1, J6.1
unnamed: F13.2, J17.1

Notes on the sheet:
Noah Bruckner
AMS Contacts
A Mode
Enderdel Adapter for testing AMS Boards



Board: 2 copper layers, 386.6 x 87.7 mm, 94 parts (12 on the bottom side), 44 nets.

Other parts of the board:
U$1, U$2, U$3, U$4, U$20, U$21, U$22, U$29, U$30, U$31: MOUNTING_M3
U$5, U$6, U$12, U$13, U$14, U$18, U$23, U$24, U$26, U$28, U$35, U$36, U$37, U$38, U$39, U$40, U$41, U$42, U$43, U$44: HV_LARGE
U$7, U$8, U$9, U$10, U$11, U$15, U$19, U$25, U$27, U$34: DANGER_HIGH_VOLTAGE
U$16, U$46: LOGO_GT_LARGE
U$17: LOGO_HYTECH_SQUARE_EXTRA_LARGE
U$32, U$45: LOGO_HYTECH_EXTRA_LARGE
U$33: NUMBER

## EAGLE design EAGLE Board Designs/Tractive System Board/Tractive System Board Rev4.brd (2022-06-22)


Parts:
C2: CAPACITOR_2220_630V_0.1UF; 2220-CAP
C3: CAPACITOR_2220_630V_1UF; 2220-CAP
C4, C11: CAPACITOR_1206_250V_0.1UF; 1206-CAP
C5, C8, C109: CAPACITOR_2220_250V_1UF; 2220-CAP
C7, C15, C16: CAPACITOR_0603_10V_10NF; 0603-CAP
C12: CAPACITOR_0805_25V_22UF; 0805-CAP
C13: CAPACITOR_0603_25V_1UF; 0603-CAP
C14: CAPACITOR_0603_25V_0.1UF; 0603-CAP
C17, C18, C19, C20, C21, C22, C103, C107: CAPACITOR_0603_10V_1UF; 0603-CAP
C102, C108: CAPACITOR_0603_10V_0.1UF; 0603-CAP
D3: SCHOTTKY_SOD323_30V; SOD-323
D4: LED_0603_BLUE; 0603-LED
D102: RECTIFIER_400V_SOD123; SOD123F
L3: INDUCTOR_SRU1048_330UH; SRU1048
R2: RESISTOR_0603_39; 0603-RES
R5: RESISTOR_0603_10K; 0603-RES
R6: RESISTOR_0603_1K; 0603-RES
R11, R12: RESISTOR_0603_HV750K; 0603-RES
R14, R15: RESISTOR_0603_360K; 0603-RES
R16, R17, R18, R19: RESISTOR_0603_HV75K; 0603-RES
R20, R21: RESISTOR_0603_33.2K; 0603-RES
R107: RESISTOR_0603_75K; 0603-RES
R108: RESISTOR_0603_8.35K; 0603-RES
R109: RESISTOR_0603_13.3K; 0603-RES
R110: RESISTOR_0805_976K; 0805-RES
R112: RESISTOR_0805_HV365K; 0805-RES
R113: RESISTOR_0603_3.32K; 0603-RES
TP9, TP12, TP13: TEST_POINT; MICRO_MINIATURE
U1: LTC3639; MSE16(12)
U2, U3: ISO224B_AIRGAP; SOIC-08(WIDE,0.295")-AIRGAP
U102: VOLTAGE_REGULATOR_ADJ_LR8_DPAK; DPAK(2-7K1S)

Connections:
+5V: C102.1, C103.1, C107.1, C108.1, U2.8 (VDD2), U3.8 (VDD2); also elsewhere on the board
GND: C102.2, C103.2, C107.2, C108.2, U2.5 (GND2), U3.5 (GND2); also elsewhere on the board
IP+: U3.7 (OUTP); also elsewhere on the board
IP-: U3.6 (OUTN); also elsewhere on the board
IT+: U2.7 (OUTP); also elsewhere on the board
IT-: U2.6 (OUTN); also elsewhere on the board
LR8_O: C4.1, C5.1, D3.A, D102.A, R5.1, R113.2, TP9.1, U102.2 (OUT)
unnamed: R11.1, R14.2
unnamed: R108.2, R109.1, U1.12 (OVLO)
unnamed: R109.2, R110.1, U1.14 (RUN)
unnamed: R12.1, R15.2
unnamed: R112.2, R113.1, U102.3 (ADJ)
unnamed: C2.1, C3.1, D102.C, R2.2, U102.1 (IN)
unnamed: D4.2 (A), R6.1
unnamed: C7.2, R5.2
unnamed: C7.1, C8.1, C11.1, C109.1, D3.C, R110.2, U1.3 (VDD)
unnamed: C15.1, R20.2, U3.2 (IN)
unnamed: C16.1, R21.2, U2.2 (IN)
unnamed: R107.2, U1.11 (ISET)
unnamed: L3.1, U1.1 (SW)
unnamed: C19.1, U3.1 (VCAP)
unnamed: C20.1, U2.1 (VCAP)
unnamed: U1.7 (VPRG1), U1.10 (SS)
PACK+FUSED: R11.2; also elsewhere on the board
P_DO: R14.1, R16.2, R18.2, R20.1, TP13.1
TS+5V: C12.1, C13.1, C14.1, C17.1, C18.1, C21.1, C22.1, L3.2, R6.2, U1.9 (VFB), U2.3 (VDD1), U3.3 (VDD1); also elsewhere on the board
TS+FUSED: R2.1, R12.2; also elsewhere on the board
TS-FUSED: C2.2, C3.2, C4.2, C5.2, C8.2, C11.2, C12.2, C13.2, C14.2, C15.2, C16.2, C17.2, C18.2, C19.2, C20.2, C21.2, C22.2, C109.2, D4.1 (C), R16.1, R17.1, R18.1, R19.1, R107.1, R108.1, R112.1, U1.6 (VPRG2), U1.8 (GND), U1.16 (GND), U2.4 (GND1), U3.4 (GND1); also elsewhere on the board
TS_DO: R15.1, R17.2, R19.2, R21.1, TP12.1

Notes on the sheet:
Precharger Power Stage
Precharger Isoamps
Shunt resistor rated to 50 mA
Overvoltage: 145V Undervoltage: 56V


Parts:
C1: CAPACITOR_POLAR__3600UF; EKYC*MM
C6, C9: CAPACITOR_2220_630V_1UF; 2220-CAP
C10: CAPACITOR_2220_630V_0.1UF; 2220-CAP
C23: CAPACITOR_0603_10V_0.1UF; 0603-CAP
C110: CAPACITOR_0603_25V_10UF; 0603-CAP
C111: CAPACITOR_0603_25V_1UF; 0603-CAP
C112: CAPACITOR_0603_35V_0.1UF; 0603-CAP
D1: LED_0603_BLUE; 0603-LED
D2: LED_0603_RED; 0603-LED
D7: LED_0603_WHITE; 0603-LED
K100: RELAY_SOLIDSTATE_NC_AG; DIP-4_AIRGAP
L1: INDUCTOR_PA4334_3.6UH; PA4334
L2: INDUCTOR_WELMHI_56UH; WE-LMHI
R1, R4, R27, R106: RESISTOR_0603_1K; 0603-RES
R3: RESISTOR_0603_1.62; 0603-RES
R101: RESISTOR_0603_75K; 0603-RES
R103: RESISTOR_0805_1M; 0805-RES
R105: RESISTOR_0805_523K; 0805-RES
R111: RESISTOR_0603_DNP; 0603-RES
U101: LTC6994-2; SOT-23-6
U103: DCM4623TD2J13D0T70; DCM4623
XF1: FUSE_HOLDER_MINIBLADEPTH; 3568

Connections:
+5V: C23.1, R105.2, U101.5 (V+); also elsewhere on the board
DCDC+: R1.2, XF1.3 (2), XF1.4 (2); also elsewhere on the board
DCDC-: C1.- (MINUS), C110.1, C111.1, C112.1, D1.1 (C), U103.7 (-OUT), U103.9 (-OUT); also elsewhere on the board
DCDC_ENABLE: U101.1 (IN); also elsewhere on the board
ENABLE: K100.4 (CONTACT2), U103.3 (EN)
GND: C23.2, D7.1 (C), K100.2 (CONTROL-), R101.1, R103.1, U101.2 (GND); also elsewhere on the board
unnamed: R103.2, R105.1, U101.6 (DIV)
unnamed: K100.1 (CONTROL+), R106.2
unnamed: R101.2, U101.3 (SET)
unnamed: R27.2, R106.1, U101.4 (OUT)
unnamed: D7.2 (A), R27.1
unnamed: D1.2 (A), R1.1
unnamed: L1.2, R3.1
unnamed: C6.1, C9.1, C10.1, L1.1, L2.1, U103.1 (+IN)
unnamed: D2.2 (A), R4.2
unnamed: R4.1, U103.4 (FLT)
unnamed: R111.1, U103.2 (TR)
unnamed: C1.+ (PLUS), C110.2, C111.2, C112.2, U103.6 (+OUT), U103.8 (+OUT), XF1.1, XF1.2 (1)
TS+FUSED: L2.2, R3.2; also elsewhere on the board
TS-FUSED: C6.2, C9.2, C10.2, D2.1 (C), K100.3 (CONTACT1), R111.2, U103.5 (-IN); also elsewhere on the board

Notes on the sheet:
350V to 12V DC-DC Converter
DC-DC Converter Enable Logic
Opto-isolator with a cutout
Info


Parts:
C100: CAPACITOR_0603_25V_0.1UF; 0603-CAP
C101: CAPACITOR_0603_10V_4.7UF; 0603-CAP
C104: CAPACITOR_0603_25V_1UF; 0603-CAP
C105, C106: CAPACITOR_0603_10V_0.1UF; 0603-CAP
D5: TVS_8V; SOT-23
D6, D9: LED_0603_BLUE; 0603-LED
D8: LED_0603_YELLOW; 0603-LED
D10: LED_0603_GREEN; 0603-LED
D11: LED_0603_ORANGE; 0603-LED
D100, D101: SCHOTTKY_SOD323_30V; SOD-323
F1, F2: FUSE_0885_1.25; 0885
J1: CONNECTOR-4__; MOLEX_MICROFIT_PTH_VERTICAL_04_DUAL
J2: CONNECTOR-5_MICRO_V6S_; MOLEX_MICROFIT_PTH_VERTICAL_06_SINGLE_SPACED
J3: CONNECTOR-5_MICRO_V7S_; MOLEX_MICROFIT_PTH_VERTICAL_07_SINGLE_SPACED
J4: CONNECTOR-8_S_S; FLEX_STACK_PTH_08_DUAL
K1: RELAY_SPST_NO_3550_12; 335X
K2: RELAY_SPST_NC_POLARIZED_3550_12; 335X
K3: RELAY_SOLIDSTATE_NO_AG; DIP-4_AIRGAP
Q1: TRANSISTOR_N_MOS__PMV15ENEA; SOT-23
R7, R8, R13: RESISTOR_B20_10K; B20
R9: RESISTOR_0603_180; 0603-RES
R10: RESISTOR_B20_750; B20
R22: RESISTOR_0603_39; 0603-RES
R23: RESISTOR_0603_10K; 0603-RES
R24: RESISTOR_0603_10; 0603-RES
R25, R26, R28, R29, R30, R31: RESISTOR_0603_1K; 0603-RES
R100: RESISTOR_0805_1M; 0805-RES
R102: RESISTOR_0805_523K; 0805-RES
R104: RESISTOR_0603_75K; 0603-RES
TP1, TP2, TP3, TP4, TP5, TP6, TP7, TP8, TP10, TP11, TP14, TP15, TP16, TP17, TP18, TP19, TP20, TP21, TP22: TEST_POINT; MICRO_MINIATURE
U4: VOLTAGE_REGULATOR_SOT223_5V; SOT223
U100: LTC6994-2; SOT-23-6

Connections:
+5V: C101.1, C105.1, C106.1, R26.1, R102.2, TP20.1, U4.2 (OUT), U4.4 (OUT), U100.5 (V+); also elsewhere on the board
+12V: C100.1, C104.1, J4.1, R25.2, TP19.1, U4.3 (IN)
DCDC+: J1.1, J1.3, TP1.1; also elsewhere on the board
DCDC-: J1.2, J1.4, TP2.1; also elsewhere on the board
DCDC_ENABLE: D5.3 (C), R23.2, R24.1, R28.2, U100.4 (OUT); also elsewhere on the board
GND: C100.2, C101.2, C104.2, C105.2, C106.2, D5.1 (A), D6.1 (C), D8.1 (C), D9.1 (C), D10.1 (C), D11.1 (C), D100.A, J4.4, K2.3 (COIL-), K3.2 (CONTROL-), Q1.2 (S), R23.1, R100.1, R104.1, TP22.1, U4.1 (GND), U100.2 (GND); also elsewhere on the board
IP+: J4.5, TP15.1; also elsewhere on the board
IP-: J4.6, TP14.1; also elsewhere on the board
IT+: J4.7, TP16.1; also elsewhere on the board
IT-: J4.8, TP17.1; also elsewhere on the board
LED+: J2.3, R9.2
unnamed: Q1.1 (G), R24.2
unnamed: R104.2, U100.3 (SET)
unnamed: R100.2, R102.1, U100.6 (DIV)
unnamed: D10.2 (A), R29.1
unnamed: D8.2 (A), R28.1
unnamed: D6.2 (A), R25.1
unnamed: D9.2 (A), R26.2
unnamed: D11.2 (A), R30.1
unnamed: D101.A, K1.3 (COIL-), Q1.3 (D)
unnamed: K1.4 (CONTACT2), R10.1
unnamed: K2.4 (CONTACT2), R13.2
unnamed: K3.1 (CONTROL+), R31.1
unnamed: K3.3 (CONTACT1), R22.2
PACK+: J3.5, K1.1 (CONTACT1), K3.4 (CONTACT2), TP6.1
PACK+FUSED: R22.1, TP8.1; also elsewhere on the board
PRECHARGE_OK: J4.3, R29.2, TP18.1, U100.1 (IN)
SHDN: D100.C, D101.C, J4.2, K1.2 (COIL+), K2.2 (COIL+), R30.2, R31.2, TP21.1
TS+5V: R9.1, TP3.1; also elsewhere on the board
TS+FUSED: F1.2, J3.4; also elsewhere on the board
TS+UNFUSED: F1.1, J3.1, J3.2, K2.1 (CONTACT1), R7.1, R10.2, TP10.1
TS-FUSED: F2.2, J2.1, J2.2, TP7.1; also elsewhere on the board
TS-UNFUSED: F2.1, J2.5, R8.1, R13.1, TP11.1
TSMP+: J3.3, R7.2, TP4.1
TSMP-: J2.4, R8.2, TP5.1

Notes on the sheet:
PACK+ Optoisolator
Precharge Relay
Discharge Relay
TSMP and TS Fusing
Power Regulation
Shunt resistor rated to 50 mA


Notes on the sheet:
10A Mini-Blade Fuse
Molex Microfit 4-pin
Molex Microfit 6-pin, spaced
Molex Microfit 7-pin, spaced
Flex Stack Board Connector



Board: 4 copper layers, 206.7 x 150.3 mm, 183 parts (37 on the bottom side), 67 nets.

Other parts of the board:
$$$$$$U$5: HV_LARGE
$$$$$$U$6: HV_1.00"
$$$$$$U$7, $$$$$$U$8, $$$$$$U$9: MOUNTING_M3
$$$$$$U$10: HV_0.50"
$$$$U$1, $$$$U$2, $$$$U$3, $$$$U$4, $$$$U$6, $$$$U$9, $$$$U$10, $$$$U$13, $$$$U$18, $$$$U$19: MOUNTING_M3
$$$$U$5, $$$$U$8, $$$$U$15, $$$$U$17: GLV
$$$$U$7: LOGO_HYTECH_SQUARE_0.28"
$$$$U$11: HV_0.50"
$$$$U$12: HV_LARGE
$$$$U$14, $$$$U$16: TS
$$U$1: TS
$$U$2, $$U$3, $$U$5, $$U$6: MOUNTING_M3
$$U$4: GLV
$$U$7: LOGO_GT_0.50"
U$1, U$6: GLV
U$5, U$7, U$11, U$12: TS
U$8: LOGO_HYTECH_MEDIUM
U$9: MOUNTING_M3
U$10: HV_0.50"
U$100: LOGO_HYTECH_EXTRA_LARGE
U$101: LOGO_GT_LARGE

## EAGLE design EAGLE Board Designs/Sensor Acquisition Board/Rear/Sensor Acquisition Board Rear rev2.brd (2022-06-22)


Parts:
A2: ESP32
C1: CAPACITOR_0603_10V_0.1UF; 0603-CAP
C2: CAPACITOR_0603_10V_1UF; 0603-CAP
C3: CAPACITOR_0603_10V_4.7UF; 0603-CAP
C4: CAPACITOR_0603_25V_1UF; 0603-CAP
D1, D2, D3: LED_0603_RED; 0603-LED
J1: JUMPER_0603_; 0603-RES
J2, J3, J4, J5: CONNECTOR-4_μF_S_RA_; MOLEX_MICROFIT_SMD_RIGHTANGLE_04_DUAL
J6: CONNECTOR-CAN_μF_S_RA_; MOLEX_MICROFIT_SMD_RIGHTANGLE_04_DUAL
R1: RESISTOR_0603_1K; 0603-RES
R2, R12: RESISTOR_0603_470; 0603-RES
R3, R5, R7, R9, R11: RESISTOR_0603_10K; 0603-RES
R4, R6, R8, R10: RESISTOR_0603_12K; 0603-RES
U2: MCP2562FD; SOIC-08(NARROW,0.15")
U3: VOLTAGE_REGULATOR_SOT-223_5V; SOT-223

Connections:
+5V: A2.USB ((USB)VIN), C1.2, C2.2, C3.1, D1.2 (A), J2.1, J3.1, J4.1, J5.1, U2.3 (VDD), U3.2 (OUT), U3.4 (OUT)
+12V: C4.1, J6.1 (+12V), U3.3 (IN)
AMB_HUM: A2.D32 (A7), R10.2, R11.1
AMB_TEMP: A2.A4 (A4(GPI)), R8.2, R9.1
BAT: A2.BAT
CANH: J1.1, J6.4 (CANH), U2.7 (CANH)
CANL: J1.2, J6.3 (CANL), U2.6 (CANL)
CAN_LED: A2.D13 (A12), D2.2 (A)
EN: A2.EN
ESP_3.3V: A2.3.3V, U2.5 (VIO)
GND: A2.GND, C1.1, C2.1, C3.2, C4.2, J2.4, J3.4, J4.4, J5.4, J6.2 (GND), R1.2, R2.2, R3.1, R4.1, R6.1, R8.1, R10.1, R12.2, U2.2 (GND), U3.1 (GND)
unnamed: D1.1 (C), R1.1
unnamed: D2.1 (C), R2.1
unnamed: R3.2, U2.8 (STBY)
unnamed: A2.TX (CTX), U2.1 (TXD)
unnamed: J2.2, J2.3, R5.2
unnamed: J4.2, J4.3, R9.2
unnamed: J3.2, J3.3, R7.2
unnamed: A2.RX (CRX), U2.4 (RXD)
unnamed: J5.2, J5.3, R11.2
unnamed: D3.1 (C), R12.1
QUEUE_LED: A2.D12 (A11(PD)), D3.2 (A)
RST: A2.RST
SUSP_BL: A2.A3 (A3(GPI)), R6.2, R7.1
SUSP_BR: A2.A2 (A2(GPI)), R4.2, R5.1

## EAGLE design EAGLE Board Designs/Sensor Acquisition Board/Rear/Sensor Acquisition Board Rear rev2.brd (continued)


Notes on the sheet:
Headers, nanofit receptacles, crimps, and esp32 to order


Board: 2 copper layers, 92.7 x 50.8 mm, 34 parts (0 on the bottom side), 22 nets.

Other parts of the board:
$$U$6: MOUNTING_M3
U$1, U$2, U$5: MOUNTING_M3
U$3: LOGO_GT_0.25"
U$4: LOGO_HYTECH_MEDIUM

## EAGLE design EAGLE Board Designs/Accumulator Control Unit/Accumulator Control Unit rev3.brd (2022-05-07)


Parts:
3.3V: LED_0603_GREEN; 0603-LED
5V: LED_0603_BLUE; 0603-LED
12V: LED_0603_RED; 0603-LED
A1: VOLTAGE_REGULATOR_MODULE_OKI-78SR_5V; OKI-78SR
C24, C33: CAPACITOR_0603_25V_10UF; 0603-CAP
C36, C103: CAPACITOR_0603_10V_4.7UF; 0603-CAP
C37: CAPACITOR_0603_10V_1UF; 0603-CAP
C100: CAPACITOR_0603_10V_10NF; 0603-CAP
C101, C104: CAPACITOR_0603_25V_1UF; 0603-CAP
C102: CAPACITOR_0603_25V_0.1UF; 0603-CAP
CURRENT_REF: TEST_POINT; MICRO_MINIATURE
CURRENT_SENSE: TEST_POINT; MICRO_MINIATURE
D8, D100, D101: TVS_15V; SOT-23
F1, F2: FUSE_0603_.75A; 0603-FUSE
J2: CONNECTOR-8_MF_T_V_; MOLEX_MICROFIT_PTH_VERTICAL_08_DUAL
J3: CONNECTOR-14_MF_T_V_; MOLEX_MICROFIT_PTH_VERTICAL_14_DUAL
J5: CONNECTOR-12_MF_T_V_; MOLEX_MICROFIT_PTH_VERTICAL_12_DUAL
J6: CONNECTOR-CAN_μF_S_RA_; MOLEX_MICROFIT_SMD_RIGHTANGLE_04_DUAL
J100: CONNECTOR-8_S_S; FLEX_STACK_PTH_08_DUAL
Q100, Q101: TRANSISTOR_N_MOS__PMV15ENEA; SOT-23
R10, R11, R19: RESISTOR_0603_1K; 0603-RES
R15: RESISTOR_0603_2.2K; 0603-RES
R61, R62: RESISTOR_0603_2K; 0603-RES
R100, R101, R102, R106: RESISTOR_0603_10K; 0603-RES
R103, R104: RESISTOR_0603_10; 0603-RES
R105: RESISTOR_0603_43K; 0603-RES
TP_3.3V, TP_5V, TP_12V: TEST_POINT; MICRO_MINIATURE
TP_GND: TEST_POINT; MICRO_MINIATURE
TP_TSAL_GREEN: TEST_POINT; MICRO_MINIATURE
TP_TSAL_RED: TEST_POINT; MICRO_MINIATURE
TSAL_GREEN: LED_0603_GREEN; 0603-LED
TSAL_RED: LED_0603_RED; 0603-LED
U26: VOLTAGE_REGULATOR_SOT223_3.3V; SOT223
U100: ADG1423; MSOP-10
U101: LM555; SOIC-08(NARROW,0.15")
XF1: FUSE_HOLDER_MINIBLADEPTH; 3568

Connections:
12VIN: D8.3 (C), J5.1, XF1.1, XF1.2 (1)
60V_THRESHOLD: U100.6 (IN), U100.7 (IN); also elsewhere on the board
+3V3: 3.3V.2 (A), C36.1, TP_3.3V.1, U26.2 (OUT), U26.4 (OUT); also elsewhere on the board
+5V: 5V.2 (A), A1.3 (OUT), C33.1, C37.1, J3.5, TP_5V.1, U26.3 (IN); also elsewhere on the board
+12V: 12V.2 (A), A1.1 (IN), C24.1, C101.1, C102.1, C104.1, J2.1, J3.7, J6.1 (+12V), J100.5, R61.1, R62.1, R106.2, TP_12V.1, U100.1 (S), U100.2 (S), U100.5 (VDD), U101.8 (VCC), XF1.3 (2), XF1.4 (2); also elsewhere on the board
ACCUMULATOR_GND: J2.7, J3.14
AIR2-: J3.13; also elsewhere on the board
AMS_OK: J5.6; also elsewhere on the board
BSPD_CURRENT: J5.10; also elsewhere on the board
CANH: J3.3, J5.9, J6.4 (CANH); also elsewhere on the board
CANL: J3.2, J5.8, J6.3 (CANL); also elsewhere on the board
CHASSIS_GND: J2.6, J5.11
CURRENT: CURRENT_SENSE.1, J3.8; also elsewhere on the board
CURRENT_REF: CURRENT_REF.1, J3.9; also elsewhere on the board
GND: A1.2 (GND), C24.2, C33.2, C36.2, C37.2, C100.2, C101.2, C102.2, C103.2, C104.2, D8.1 (A), D100.1 (A), D101.1 (A), J2.4, J3.4, J3.6, J3.11, J5.2, J6.2 (GND), J100.8, Q100.2 (S), Q101.2 (S), R10.1, R11.1, R15.1, R19.1, R100.1, R101.2, R102.2, TP_GND.1, U26.1 (GND), U100.4 (GND), U100.8 (GND), U101.1 (GND); also elsewhere on the board
IMD_OK: J5.7; also elsewhere on the board
ISO_PACK+: J100.1; also elsewhere on the board
ISO_PACK-: J100.2; also elsewhere on the board
ISO_TS+: J100.3; also elsewhere on the board
ISO_TS-: J100.4; also elsewhere on the board
MHS: J2.3, R15.2; also elsewhere on the board
unnamed: 3.3V.1 (C), R19.2
unnamed: 5V.1 (C), R10.2
unnamed: C103.1, R105.1, U101.2 (TRIGGER), U101.6 (THRESHOLD)
unnamed: C100.1, U101.5 (CONTROL)
unnamed: R105.2, R106.1, U101.7 (DISCHARGE)
unnamed: 12V.1 (C), R11.2
unnamed: D100.3 (C), R102.1, R104.1, TP_TSAL_GREEN.1, U100.9 (D)
unnamed: D101.3 (C), R101.1, R103.1, TP_TSAL_RED.1, U101.3 (OUTPUT)
unnamed: R62.2, TSAL_GREEN.2 (A)
unnamed: F2.1, J5.3
unnamed: F1.1, J5.4
unnamed: R61.2, TSAL_RED.2 (A)
unnamed: Q100.1 (G), R103.2
unnamed: Q101.1 (G), R104.2
OKHS: J2.2; also elsewhere on the board
PRECHARGE_OK: J100.7; also elsewhere on the board
SHDN: J3.10, J3.12, J5.5, J100.6
TIMER_EN: R100.2, U100.10 (D), U101.4 (!RESET)
TSAL_GREEN: F2.2, Q101.3 (D), TSAL_GREEN.1 (C)
TSAL_RED: F1.2, Q100.3 (D), TSAL_RED.1 (C)

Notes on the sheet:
Josh Kirshenbaum
Connectors
ACU to TSB connections
Power, CAN, TSAL, Shutdown Signals
Power Fusing and Regulation
SHDN connnects directly to AIR+, AIR- connects directly to GND
TSAL Circuitry
555 Timer Astable Mode Frequency: 3.529 Hz Duty Cycle: 50.57% Rules say 2-5Hz
SHDN connnects directly to AIR+
Energy Meter, Current Sensor Accumulator GND, both AIR+ and -
IMD


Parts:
AMS_OK: LED_0603_GREEN; 0603-LED
D2: TVS_8V; SOT-23
IMD_OK: LED_0603_ORANGE; 0603-LED
OKHS: LED_0603_YELLOW; 0603-LED
Q1: TRANSISTOR_N_MOS__PMV15ENEA; SOT-23
R2, R7, R8: RESISTOR_0603_2K; 0603-RES
R3, R9: RESISTOR_0603_1K; 0603-RES
R6, R12, R14: RESISTOR_0603_10K; 0603-RES
R13: RESISTOR_0603_10; 0603-RES
TP_AMS_OK: TEST_POINT; MICRO_MINIATURE
TP_IMD_OK: TEST_POINT; MICRO_MINIATURE
U1, U2: RELAY_SOLIDSTATE_NO; DIP-4

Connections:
+12V: R7.2, U1.4 (CONTACT2), U2.4 (CONTACT2); also elsewhere on the board
AMS_OK: AMS_OK.2 (A), R12.2, TP_AMS_OK.1, U2.3 (CONTACT1); also elsewhere on the board
AMS_OK_3.3V: D2.3 (C), R13.1, R14.1; also elsewhere on the board
GND: D2.1 (A), Q1.2 (S), R2.1, R3.1, R6.1, R9.1, R12.1, R14.2, U1.2 (CONTROL-); also elsewhere on the board
IMD_OK: IMD_OK.2 (A), R6.2, TP_IMD_OK.1, U1.3 (CONTACT1); also elsewhere on the board
unnamed: R8.2, U1.1 (CONTROL+)
unnamed: OKHS.1 (C), R9.2
unnamed: R7.1, U2.1 (CONTROL+)
unnamed: AMS_OK.1 (C), R3.2
unnamed: Q1.3 (D), U2.2 (CONTROL-)
unnamed: IMD_OK.1 (C), R2.2
unnamed: Q1.1 (G), R13.2
OKHS: OKHS.2 (A), R8.1; also elsewhere on the board

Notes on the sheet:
Josh Kirshenbaum
Shutdown Signal Buffering/Amplification


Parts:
C13, C14, C15, C16, C17, C18, C19, C26, C27, C28: CAPACITOR_0603_10V_0.1UF; 0603-CAP
D4: TVS_8V; SOT-23
PACK+_OUT_TEST: TEST_POINT; MICRO_MINIATURE
PRECHARGE_OK: LED_0603_RED; 0603-LED
PRECHARGE_OK_TEST: TEST_POINT; MICRO_MINIATURE
Q2: TRANSISTOR_N_MOS__PMV15ENEA; SOT-23
R16: RESISTOR_0603_1K; 0603-RES
R17, R29, R37, R42, R43, R44, R50, R52, R69, R71, R73, R81: RESISTOR_0603_10K; 0603-RES
R18: RESISTOR_0603_10; 0603-RES
R28: RESISTOR_0603_470; 0603-RES
R38, R51, R53, R66, R67, R74, R75: RESISTOR_0603_11.5K; 0603-RES
R39: RESISTOR_0603_84.5K; 0603-RES
R40, R45, R47, R54, R64: RESISTOR_0603_DNP; 0603-RES
R41, R48: RESISTOR_0603_10.2K; 0603-RES
R46: RESISTOR_0603_215K; 0603-RES
R49, R63: RESISTOR_0603_4.12K; 0603-RES
R65, R68, R72, R76: RESISTOR_0603_10.5K; 0603-RES
R70: RESISTOR_0603_11.3K; 0603-RES
TS+_OUT_TEST: TEST_POINT; MICRO_MINIATURE
U8: RELAY_SOLIDSTATE_NO; DIP-4
U11, U13, U15, U17, U21, U22, U23: OPAMP_1_CHANNEL_OPA991; SC-70-5
U12, U14, U16: LOGICGATE_AND_DCK3; SC-70-5

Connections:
0.95X_DIV: R45.2, R46.2, R70.1, U13.3 (VIN-)
0.5989V_DIV: R38.2, R39.1, R40.2, U21.3 (VIN-)
2.5_DIV: R51.2, R53.1, R54.2, U17.3 (VIN-)
3.56V_DIV_A: R41.2, R63.1, R64.1, U11.1 (VIN+)
3.56V_DIV_B: R47.1, R48.2, R49.1, U15.1 (VIN+)
60V_THRESHOLD: R37.2, U21.4 (VOUT); also elsewhere on the board
+5V: C13.1, C14.1, C15.1, C16.1, C17.1, C18.1, C19.1, C26.1, C27.1, C28.1, R39.2, R47.2, R49.2, R53.2, R63.2, R64.2, U8.4 (CONTACT2), U11.5 (VDD), U12.5 (VDD), U13.5 (VDD), U14.5 (VDD), U15.5 (VDD), U16.5 (VDD), U17.5 (VDD), U21.5 (VDD), U22.5 (VDD), U23.5 (VDD); also elsewhere on the board
AIR2-: Q2.3 (D); also elsewhere on the board
GND: C13.2, C14.2, C15.2, C16.2, C17.2, C18.2, C19.2, C26.2, C27.2, C28.2, D4.1 (A), PRECHARGE_OK.1 (C), Q2.2 (S), R17.2, R29.1, R37.1, R38.1, R40.1, R41.1, R42.1, R43.1, R44.1, R45.1, R46.1, R48.1, R50.1, R51.1, R52.1, R54.1, R68.2, R69.1, R71.1, R73.1, R76.2, R81.1, U8.2 (CONTROL-), U11.2 (GND), U12.3 (GND), U13.2 (GND), U14.3 (GND), U15.2 (GND), U16.3 (GND), U17.2 (GND), U21.2 (GND), U22.2 (GND), U23.2 (GND); also elsewhere on the board
HV+_OUT_OK: R43.2, U12.4 (OUT), U14.1 (IN1)
ISO_PACK+: R75.1; also elsewhere on the board
ISO_PACK-: R73.2, R74.1; also elsewhere on the board
ISO_TS+: R67.1; also elsewhere on the board
ISO_TS-: R66.1, R81.2; also elsewhere on the board
unnamed: PRECHARGE_OK.2 (A), R16.1
unnamed: Q2.1 (G), R18.2
unnamed: R67.2, R68.1, U22.1 (VIN+)
unnamed: R65.1, R66.2, U22.3 (VIN-)
unnamed: R75.2, R76.1, U23.1 (VIN+)
unnamed: R72.1, R74.2, U23.3 (VIN-)
unnamed: R28.1, U14.4 (OUT)
unnamed: R28.2, U8.1 (CONTROL+)
PACK+_OUT: PACK+_OUT_TEST.1, R70.2, R71.2, R72.2, U15.3 (VIN-), U17.1 (VIN+), U23.4 (VOUT); also elsewhere on the board
PRECHARGE+_OUT_OK: R29.2, U14.2 (IN2), U16.4 (OUT)
PRECHARGE_OK: D4.3 (C), PRECHARGE_OK_TEST.1, R16.2, R17.1, R18.1, U8.3 (CONTACT1); also elsewhere on the board
PRECHARGE_REACHED: R44.2, U12.2 (IN2), U13.4 (VOUT)
TS+_OUT: R65.2, R69.2, TS+_OUT_TEST.1, U11.3 (VIN-), U13.1 (VIN+), U21.1 (VIN+), U22.4 (VOUT); also elsewhere on the board
TS+_OUT_OV_OK: R42.2, U11.4 (VOUT), U12.1 (IN1)
V_PACK_REF_OV_OK: R50.2, U15.4 (VOUT), U16.1 (IN1)
V_PACK_REF_UV_OK: R52.2, U16.2 (IN2), U17.4 (VOUT)

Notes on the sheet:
60V threshold check
At 60V on the input, the output is 0.5999986V. To ensure that we trip by 60V, the divider has been downsized to 0.5989V instead of nominal 0.6V. The DNP resistor is included for ease of tuning the voltage divider.
0.95x
low side switches shutdown current across precharge relay
Josh Kirshenbaum
AIR2- Low Side Switching with PRECHARGE_OK


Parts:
BSPD_CURRENT: TEST_POINT; MICRO_MINIATURE
C2, C8, C20, C29, C35: CAPACITOR_0603_25V_0.1UF; 0603-CAP
C3, C9, C10, C11, C21, C22, C30, C31: CAPACITOR_0603_10V_0.1UF; 0603-CAP
C4, C12, C23, C32: CAPACITOR_0603_10V_680PF; 0603-CAP
R22, R30, R55, R59, R77: RESISTOR_0603_10K; 0603-RES
R23, R31, R56, R78: RESISTOR_0603_12K; 0603-RES
R57: RESISTOR_0603_1K; 0603-RES
R58: RESISTOR_0603_1.4K; 0603-RES
U3, U9, U18, U20, U24: OPAMP_1_CHANNEL_OPA991; SC-70-5
U4, U10, U19, U25: MAX7404; SOIC-08(NARROW,0.15")

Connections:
+3V3: C2.1, C8.1, C9.1, C10.1, C20.1, C21.1, C29.1, C30.1, U3.5 (VDD), U4.4 (VDD), U4.7 (!SHDN), U9.5 (VDD), U10.4 (VDD), U10.7 (!SHDN), U18.5 (VDD), U19.4 (VDD), U19.7 (!SHDN), U24.5 (VDD), U25.4 (VDD), U25.7 (!SHDN); also elsewhere on the board
+12V: C35.1, U20.5 (VDD); also elsewhere on the board
BSPD_CURRENT: BSPD_CURRENT.1, R58.2, U20.4 (VOUT); also elsewhere on the board
CURRENT: R30.1, R59.2, U20.1 (VIN+); also elsewhere on the board
CURRENT_BUFFER: U9.3 (VIN-), U9.4 (VOUT), U10.2 (IN)
CURRENT_FILTERED: U10.5 (OUT); also elsewhere on the board
CURRENT_REF: R22.1; also elsewhere on the board
CURRENT_REF_BUFFER: U3.3 (VIN-), U3.4 (VOUT), U4.2 (IN)
CURRENT_REF_FILTERED: U4.5 (OUT); also elsewhere on the board
GND: C2.2, C3.2, C4.2, C8.2, C9.2, C10.2, C11.2, C12.2, C20.2, C21.2, C22.2, C23.2, C29.2, C30.2, C31.2, C32.2, C35.2, R23.2, R31.2, R56.2, R57.1, R59.1, R78.2, U3.2 (GND), U4.3 (GND), U9.2 (GND), U10.3 (GND), U18.2 (GND), U19.3 (GND), U20.2 (GND), U24.2 (GND), U25.3 (GND); also elsewhere on the board
unnamed: R57.2, R58.1, U20.3 (VIN-)
unnamed: C31.1, U25.1 (COM), U25.6 (OS)
unnamed: C32.1, U25.8 (CLK)
unnamed: R77.2, R78.1, U24.1 (VIN+)
unnamed: C11.1, U10.1 (COM), U10.6 (OS)
unnamed: C12.1, U10.8 (CLK)
unnamed: R30.2, R31.1, U9.1 (VIN+)
unnamed: C3.1, U4.1 (COM), U4.6 (OS)
unnamed: C4.1, U4.8 (CLK)
unnamed: R22.2, R23.1, U3.1 (VIN+)
unnamed: C22.1, U19.1 (COM), U19.6 (OS)
unnamed: C23.1, U19.8 (CLK)
unnamed: R55.2, R56.1, U18.1 (VIN+)
PACK+_BUFFER: U18.3 (VIN-), U18.4 (VOUT), U19.2 (IN)
PACK+_FILTERED: U19.5 (OUT); also elsewhere on the board
PACK+_OUT: R55.1; also elsewhere on the board
TS+_OUT: R77.1; also elsewhere on the board
TS+_OUT_BUFFER: U24.3 (VIN-), U24.4 (VOUT), U25.2 (IN)
TS+_OUT_FILTERED: U25.5 (OUT); also elsewhere on the board

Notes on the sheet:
Josh Kirshenbaum
Analog Filtering

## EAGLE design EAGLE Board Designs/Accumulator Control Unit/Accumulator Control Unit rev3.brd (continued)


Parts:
A2: TEENSY_4.0; TEENSY_SHORT
C1, C6: CAPACITOR_0603_10V_10NF; 0603-CAP
C5, C34, C38: CAPACITOR_0603_10V_0.1UF; 0603-CAP
C25: CAPACITOR_0603_10V_4.7NF; 0603-CAP
C39: CAPACITOR_0603_10V_1UF; 0603-CAP
D3, D7, D9, D10, D11: TVS_15V; SOT-23
J1: CONNECTOR-2_MF_T_V_; MOLEX_MICROFIT_PTH_VERTICAL_02_SINGLE
J4: JUMPER__1X02; 1X02
R1: RESISTOR_0603_120; 0603-RES
R4, R20, R79, R108, R110: RESISTOR_0603_; 0603-RES
R5, R80, R107: RESISTOR_0603_12K; 0603-RES
R21: RESISTOR_0603_15K; 0603-RES
R24, R25: RESISTOR_0603_1K; 0603-RES
R26, R27, R82: RESISTOR_0603_10K; 0603-RES
R32, R33: RESISTOR_0603_2K; 0603-RES
R34, R35: RESISTOR_0603_470; 0603-RES
R36, R60: RESISTOR_0603_60.4; 0603-RES
R109: RESISTOR_0603_18.7K; 0603-RES
T1: TRANSFORMER_HM2112ZNLT_AIRGAP; HM2112ZNLT_AIRGAP
TD+: TEST_POINT; MICRO_MINIATURE
TD-: TEST_POINT; MICRO_MINIATURE
TEENSY_OK: LED_0603_RED; 0603-LED
U5: LTC6820; MSOP-16
U6: LOGICGATE_BUFFER; SC-70-5
U7: ADM8316WBX30; SOT-23-5
U27: TCAN1051HQV-Q1; SOIC-08(NARROW,0.15")
WATCHDOG: LED_0603_BLUE; 0603-LED
WATCHDOG_OK: TEST_POINT; MICRO_MINIATURE

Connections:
12V_SCALED_3.3V: A2.D19 (A5), R107.1, R108.2
+3V3: A2.3.3V, C5.1, C6.2, C34.2, R32.2, R33.2, U5.1 (VDD), U5.6 (VLOGIC), U5.7 (VDD), U5.8 (VDD), U5.9 (VDD), U5.12 (VDD), U6.5 (VDD), U27.5 (VIO); also elsewhere on the board
+5V: A2.VIN, C38.2, C39.2, U27.3 (VDD); also elsewhere on the board
+12V: D7.3 (C), R108.1; also elsewhere on the board
AMS_OK_3.3V: U6.4 (OUT); also elsewhere on the board
BSPD_CURRENT: D9.3 (C), R79.1; also elsewhere on the board
BSPD_CURRENT_TEENSY: A2.D22 (A8), R79.2, R80.1
CANH: J4.1, U27.7 (CANH); also elsewhere on the board
CANH/1.3B: J4.2, R36.2
CANL: R60.2, U27.6 (CANL); also elsewhere on the board
CS_LTC_6820: A2.D10 ((CS)D10), U5.5 (!CS)
CURRENT_FILTERED: A2.D21 (A7); also elsewhere on the board
CURRENT_REF_FILTERED: A2.D20 (A6); also elsewhere on the board
GND: A2.AGND/GND (GND), A2.GND, C1.2, C5.2, C6.1, C25.1, C34.1, C38.1, C39.1, D3.1 (A), D7.1 (A), D9.1 (A), D10.1 (A), D11.1 (A), R5.2, R21.2, R24.2, R26.1, R80.2, R82.1, R107.2, R110.2, TEENSY_OK.1 (C), U5.13 (GND), U5.14 (GND), U6.3 (GND), U7.2 (GND), U27.2 (GND), U27.8 (S), WATCHDOG.1 (C); also elsewhere on the board
IM: T1.10 (TD-), U5.10 (IM)
IMD_OK: D10.3 (C), R4.1; also elsewhere on the board
IMD_OK_TEENSY: A2.D16 (A2), R4.2, R5.1
IP: T1.12 (TD+), U5.11 (IP)
MHS: D3.3 (C), R20.1; also elsewhere on the board
MHS_TEENSY: A2.D14 (A0), R20.2, R21.1
unnamed: A2.D11 ((SDO)D11), R33.1, U5.2 (SDI)
unnamed: R82.2, U6.2 (IN), U7.1 (!RESET!)
unnamed: C25.2, R36.1, R60.1
unnamed: A2.D0 ((CRX1)D0), A2.D4, U27.4 (RXD)
unnamed: A2.D1 ((CTX1)D1), A2.D3, U27.1 (TXD)
unnamed: R25.1, U5.16 (IBIAS)
unnamed: R24.1, R25.2, U5.15 (ICMP)
unnamed: C1.1, T1.11 (TCT)
unnamed: A2.D12 ((SDI)D12), R32.1, U5.3 (SDO)
unnamed: A2.D13 ((CLK)D13), U5.4 (CLK)
unnamed: R34.1, WATCHDOG.2 (A)
unnamed: R35.1, TEENSY_OK.2 (A)
unnamed: R27.2, U7.3 (!MR!)
PACK+_FILTERED: A2.D17 (A3); also elsewhere on the board
PRECHARGE_OK: D11.3 (C), R109.1; also elsewhere on the board
PRECHARGE_OK_TEENSY: A2.D15 (A1), R109.2, R110.1
TD+: J1.1, R1.2, T1.1 (MX+), TD+.1
TD-: J1.2, R1.1, T1.3 (MX-), TD-.1
TEENSY_OK: A2.D6, R27.1, R35.2, U7.5 (VDD)
TS+_OUT_FILTERED: A2.D18 (A4); also elsewhere on the board
WATCHDOG_INPUT: A2.D5, R26.2, R34.2, U7.4 (WDI), WATCHDOG_OK.1

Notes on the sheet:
12V to 3.3V
5V to 3.3V
Watchdog Timer
Voltage Dividers
LTC6820 and Transformer
10V to 3.3V



Board: 4 copper layers, 186.7 x 143.9 mm, 241 parts (24 on the bottom side), 117 nets.

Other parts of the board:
U$1, U$5, U$8, U$9, U$10, U$11, U$12, U$14, U$16, U$17, U$18, U$19, U$20: MOUNTING_M3
U$2, U$7: GLV
U$3, U$6: TS
U$4, U$100: HV_LARGE
U$13: LOGO_HYTECH_EXTRA_LARGE
U$15: LOGO_GT_0.50"

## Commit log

2021-07-24 AMS Rev 16 Schematic (#2)
    * New bms work
    Didn't finish in one day. Screw modules
    * Finished BMS schematic
    * Minor BMS update
    * trying eagle hack
    * Resolved part cache error
    * Basic work
    * Revert "Basic work"
    This reverts commit 314f29d0700f840b339ecbc3c92328a4e326f93a.
    * Reset board design
    * Minor BMS stuff
    * bms work
    * started placing ltc6813
    * Last commit? :(
    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
    [AMS Segment rev16.brd, AMS Segment rev16.sch, BMS Cell Charging Adapter rev1.brd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]
2021-08-15 Telemetry (#13)
    * Wheel Speed Board
    * Update Wheel Speed Sensor rev1.brd
    * Removed vias
    * Moved to top layer
    * Improved board design
    * changed can transciever package
    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
    [Full Thermocouple.brd, Full Thermocouple.sch, HX711 loadcell test hytech v1.brd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]
2021-08-15 Bspd lt spice (#12)
    * LTspice files (AND,OR,OP AMP, BSPD)
    * Updated BSPD files (CURRENT, BRAKE, FULL)
    * Update .gitignore
    * I'm bad at git
    * Updated names, values, analysis
    * Completed BSPD
    * Updated BSPD_FULL
    * added the q1 transistor section and the transistor pspice files
    * Working example with other mosfet
    * Updated BSPD_FULL
    * the and gate's off resistance is too low
    * i rigged it
    * More BSPD work
    * Some design config
    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
2021-08-15 Charger controller rev 6 (#10)
    * STWD100 and SN74LVC1G08 test schematic
    * add led for WATCHDOG_OK signal
    * replace 5V with 3V3 and create board
    * Update STWD100 Charger Controller rev1.brd
    * Update STWD100 Charger Controller rev1.brd
    * Fix DRC errors in charger controller board
    * start charger controller rev 6 schematic and board
    * add watchdog_ok led, move leds on schematic, and finish board
    * add optocoupler to charget controller rev 6 shutdown circuit
    * Added Optocoupler Circuit to Board
    * rearrange cc rev 6 schematic
    * redid teensy connections
    * made additional silkscreen changes and add 2 leds
    * Started to implement the e-fuse into the charger cont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
    [Charger Control Board rev5.brd, Charger Control Board rev6.brd, Charger Control Board rev6.sch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]
2021-08-15 Sensor acquisition rev1 (#9)
    * Create Sensor Acquisition Board Rev1.sch
    Added ATMEGA328P and CAN Interface/Controller
    * Update Sensor Acquisition Board Rev1.sch
    added opamp, filter, and adc
    * Fnished schematic (completed the signal processing portion) and made board
    * Added controls and connectors
    * So close to being done (updated board)
    * Wired everything but 5V and GND
    * Finished PCB
    * Made PCB one sided
    * Switched in MAX7400 filters and MCP2515 and remade board
    * Rev2_1 schematic
    * More changes
    * Made Board good (ie. finished board)
    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
    [Sensor Acquisition Board Rev1.brd, Sensor Acquisition Board Rev1.sch, Sensor Acquisition Board Rev2.brd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]
2021-08-15 Ltc4421 l tspice (#8)
    * Add files via upload
    * Rename LTC4421 Circuit.asc to LTspice/LTC4421 Circuit.asc
    * Add files via upload
    * Delete LTC4421 Circuit.asc
    * Add files via upload
    * Rename LTC4421 Test Circuit.asc to LTspice/LTC4421 Test Circuit.asc
    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
2021-08-15 Power switching circuit (#7)
    * Rename Power Switching Circuit.brd to Power Switching Circuit rev1.brd
    * Rename Power Switching Circuit.sch to Power Switching Circuit rev1.sch
    * Delete Power Switching Circuit rev1.brd
    * Delete Power Switching Circuit rev1.sch
    * Design Review Changes
    Made the board much more compact and implemented schematic and board changes which were discussed during the 2/14 design review session
    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
    [Power Switching Circuit rev1.brd, Power Switching Circuit rev1.sch, Power Switching Circuit rev2.brd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]
2021-08-15 Bms rev 15 (#6)
    * Added aesthetic and board test point changes
    * Replaced fuses and resistors
    * Started changing the silkscreen to have reference indicators
    * Fixed silkscreen for ref ind, switched pogos for springs, altered traces
    * Finished fixing silkscreen and adding names
    * Final BMS rev15 design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
    [BMS Segment rev15.brd, BMS Segment rev15.sch]
2021-08-15 Elliptic filter (#11)
    * started the PCB tester board
    * WIP tester board outputs
    * added a SP3T switch to the library
    * WIP
    * initial schematic
    * create board and adjust schematic for different pin layout
    * Update MAX7400 Test Board.sch
    * fixed somethings apparently
    * Silkscreen changes
    * change silkscreen
    * Silkscreen changes
    * Changed DRC
    * moved chip name to bValues layer
    * Delete PCB Tester Board rev1.sch
    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
    [MAX7400 Test Board.brd, MAX7400 Test Board.sch]
2021-08-15 Merge main in (#4) (#5)
    * AMS Rev 16 Schematic (#2)
    * Moved Ethan rev15 to it's new home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
2021-09-27 Keychain rev3 (#17)
    * added rev3
    * Keychain rev3 complete
    * moved resistor positions to better reflect voltage div
    [Keychain rev3.brd, Keychain rev3.sch]
2021-11-15 New bspd resistor values (#1)
    * New bspd resistor values
    * Fixed HV board rev14 schematic note
    [HV Board rev14.sch, MainECU rev10.brd, MainECU rev10.sch]
2021-11-15 Ams rev 16 (#19)
    * Created new board, laid out springs, started laying out components
    * Fixed ERC errors
    * holder push
    * Revert "holder push"
    This reverts commit 5c5a8d45b60ff0506a7db83585d04c86d1c2f773.
    * more preliminary board layout
    * Fixed erc errors again
    * because cody wants it
    * redid preliminary board layout
    * netclasses push
    * Updated connector foorprint
    * recommit after git corrupt
    * Updated fuse and connector footprints
    * Added note about EV.8.3.2
    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
    [ADIS16209 Teensy rev1.brd, ADIS16209 Teensy rev1.sch, AMS Segment rev16.brd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]
2021-11-17 Sensor acquisition board rev3 (#22)
    * Rev3 .brd and .sch files created
    Copied directly from rev2
    * Fixed resetlow on MCP2515
    * SAB Rev3 Schematic and Board done, awaiting formal review
    * Completed shipping version of rev3
    * Added folder for order files, deleted blank sheet
    * vector font change
    * Added Name and Description to Schematic
    * Generated BOMs
    * Create IMU CAN Speed Converter Board rev1.sch
    * Update IMU CAN Speed Converter Board rev1.sch
    * Update IMU CAN Speed Converter Board rev1.sch
    * Finished IMU Board
    * Finished Design Review and Manufacturing Files
    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
    [IMU CAN Speed Converter Board rev1.brd, IMU CAN Speed Converter Board rev1.csv, IMU CAN Speed Converter Board rev1.sch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]
2021-12-03 Ams rev 16 ordering (#23)
    [AMS Segment rev16.sch]
2021-12-07 Esf circuits (#24)
    [Accumulator TS Internals.sch, Accumulator TS Schematic.sch, BSPD System Schematic.sch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]
2021-12-29 Ams rev 17 (#25)
    * all cells placed on board
    * placed ICs
    * Added netclasses, fixed resistor footprints
    * Completed layout
    * moved connectors
    * moved board dimensions out and moved holes to not int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
    [AMS Segment rev16.brd, AMS Segment rev16.sch, AMS Segment rev17 BOM.xlsx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]
2021-12-29 Cleanup (#27)
    [0805 Breakout Board.brd, 0805 Breakout Board.sch, ADIS16209 Practice Board.brd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]
2021-12-29 Lt3045 ltspice (#28)
    * experimental 3045-1 sims
    * 3990 991 magic
    * trickless
    * Added simulation for no VIOC
    * 3.3 -> 5V charge pump simulation
    * Tried regulated charge pump and didn't work
    * More sims
2022-01-05 Tractive system active light rev4 (#29)
    * TSAL rev4
    * tsal rev4
    changed led symbol, added frame, changed to common power
    * Update Tractive System Active Light rev4.sch
    * Update Tractive System Active Light rev4.sch
    * updated ked symbol, added frame
    * updated led symbol
    * updated resistor
    * Created Board, added thermal net to schematic
    * Update Tractive System Active Light rev4.brd
    * moved board closer to centered to origin
    * Update Tractive System Active Light rev4.brd
    * updated resistors, right angle connector
    * updated library
    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
    [TMCS1101A4.brd, Tractive System Active Light rev4.brd, Tractive System Active Light rev4.csv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]
2022-01-05 Dashboard rev3 (#30)
    * Copied Dashboard rev3 files from dashboard rev2
    * incomplete changes to schamatic for rev3 features
    * Updated names to wires
    * Minor deletions because of the sensor board
    * Just working on rev3
    * Dashboard rev3
    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
    [Dashboard rev2.brd, Dashboard rev2.sch, Dashboard rev3 BOM.xlsx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]
2022-01-10 Tsal mech electrical reconciliation (#31)
    * edited LED and mounting hole positions, added DXF
    * order files
    [Tractive System Active Light rev4.brd, Tractive System Active Light rev4.dxf]
2022-01-19 Esf rev2 (#32)
    * all but TSAL updated
    * some changes in response to ESF comments
    * updated all schem to comply with ESF comments
    * esf updates completed
    * added missing resistors
    [Accumulator TS Schematic.sch, BSPD System Schematic.sch, Charging Shutdown Circuit Schematic.sch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]
2022-01-20 Tractive system active light rev5 (#34)
    * Moved parts on board
    * Moved board dimensions
    * Moved connector to point down
    * move mounting holes 50 mils higher
    * extended thermal planes
    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
    [Tractive System Active Light rev5.brd, Tractive System Active Light rev5.sch]
2022-01-20 Acu rev 1 (#33)
    * Update Schematic Fields
    * initial throw everything on the schematic
    * add connectors to schematic and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
    [Accumulator Control Unit rev1 BOM.xlsx, Accumulator Control Unit rev1.brd, Accumulator Control Unit rev1.csv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]
2022-01-20 Charger controller rev 7 (#35)
    * Initial Revision 7
    Changed to teensy 4.0, removed efuse and charger control relay, added new connector for charger
    * New rev7 schematic
    Made new rev7 schematic using updated component library (work in progress)
    * Complete rev7 schematic
    Finished making rev7 schematic using new eagle parts library
    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
    [Charger Control Board rev7.brd, Charger Control Board rev7.csv, Charger Control Board rev7.sch]
2022-01-22 Tractive System Board Rev 1 and 2 (#37)
    * Created the TSB schematic, added DCDC, added precharge power, added relay logic
    * Added the rest of the connectors and fuses
    * Added board layout
    * Added low pass filters for the analog signals
    * Added comments from the schematic review
    * Added more changes from the schematic review
    * Put the schem on grid, changed little things, added info for more changes
    * added low pass filter and other stuff
    * Added comments from design review
    * Made a board
    * added adm825 circuitry, fixed connectors
    * Finished Schematic by adding shunt resistors, fixing resistor dividers, and adding OVLO and UVLO
    * Fixed the look of the schem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
    [ADIS16209 Practice Board.brd, ADIS16209 Practice Board.sch, DC DC Converter rev1.brd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]
2022-01-23 Added extra shutdown f pin to charger connector (#38)
    * Added extra shutdown f pin to charger connector
    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
    [Charger Control Board rev7.brd, Charger Control Board rev7.sch]
2022-01-23 Panel (#36)
    * minor cleanup
    * Fixes
    * removing more files that should be in sharepoint
    * 4 board to panelize
    * Fixing naming
    * Delete EAGLE Board Designs/Accumulator Management System/AMS Segment/Order files directory
    * Delete EAGLE Board Designs/Accumulator Control Unit/Order files directory
    * Delete EAGLE Board Designs/Tractive System Active Light/Order files directory
    * Delete EAGLE Board Designs/Charger Control Board/Order files directory
    * Loaded panel up
    * split panel into two
    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
    [ACU rev2 CCU rev7.brd, ACU rev2 TSB rev2 CCU rev7 TSAL rev5.brd, AMS Segment rev16.brd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]
2022-01-25 order files (#40)
    [Accumulator Control Unit rev1 BOM.xlsx, Accumulator Control Unit rev1.csv, Accumulator Control Unit rev1_top_bom.csv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]
2022-02-18 Sensor acquisition board front/rear rev1 (#41)
    * Added new folders for front and rear boards, removed deprecated rev1 and rev2
    * Placing files to begin front/rear boards
    * Created sch for front rev 1
    * Started on rear board sch
    * Created Rear board
    * TCAN to MCP on rear
    * Working on front board
    * Created front board
    * Minor Rear board changes
    * connect Ultimate GPS to SAB Front Teensy
    * Created GPS LED and added GPS to Board
    * Fixed front
    * Fixed GPS connections
    * Small changes
    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
    [Dashboard rev3 BOM.xlsx, Dashboard rev3.csv, Dashboard rev3_top_bom.csv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]
2022-03-06 revised schematics to reflect most accurate information (#44)
    [Accumulator TS Schematic.sch, BSPD System Schematic.sch, Charging Shutdown Circuit Schematic.sch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]
2022-03-21 Dashboard rev 4 (#45)
    * Added TPs for all shutdown signals
    * SSOK and Inertia Read signals connected to LED nMos switches
    * Added inertia and ssok led circuitry, flipped LED, and rerouted
    * Renamed Inertia and SSOK
    * Removed shutdown circuitry diodes
    * Cleanup up routing and test points
    * Rerouted dash leds after reorientation
    * Changed silkscreen lettering
    * Updated routing and TP naming
    * Added red-orange led for mcu led
    * Added not gates and tractive LED
    * ripup and reorder of leds
    * Began rewiring
    * Working on reconnection
    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
    [Dashboard rev4.brd, Dashboard rev4.csv, Dashboard rev4.sch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]
2022-05-07 Acu rev 3 (#48)
    * can jumper + moved some footprints
    * can jumper, tsal fuse
    * fix text
    * some changes based on checklist
    * passed review
    * Some fixes
    * added new changes based on doc
    * Revert "Some fixes"
    This reverts commit 12d1257df97418106eafc9ff778c5bcc0629b467.
    * some changes
    * some more changes
    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
    [Accumulator Control Unit rev3.brd, Accumulator Control Unit rev3.csv, Accumulator Control Unit rev3.sch]
2022-06-11 added descriptions (#49)
    [Accumulator Control Unit rev3.sch]
2022-06-22 Sab rear rev2 (#46)
    * created rev2
    * regrounded with groundplane
    * Created rear sab board
    * Fixed wire stubs
    * Fixed labeling and incorrect connections
    * Changed silkscreen
    * ordering, DRC
    * Added ordering info
    * new ordering files
    * clean up file structure
    [Dashboard rev4.sch, SAB rev3 BOM.xlsx, Sensor Acquisition Board Rear rev2.brd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]
2022-06-22 Tractive system board rev3 (#42)
    * made changes to board design
    * Finished board design
    * More final changes
    * Made specified changes to the tsb
    * Final chnages
    * Final fixes
    * Updated libraries
    * Finalized tsb rev4
    * files cleanup
    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
    [HV Board rev14.brd, HV Board rev14.sch, Tractive System Board Rev3.brd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]
2022-06-23 Enerdel adapter rev7 (#43)
    * Create BMS Enerdel Adapter rev7.sch
    * Update BMS Enerdel Adapter rev7.sch
    * Finished rev 7 schematic
    * Update BMS Enerdel Adapter rev7.sch
    * Schematic Framework Finished
    * Update BMS Enerdel Adapter rev7.brd
    * Update BMS Enerdel Adapter rev7.brd
    * Matched enerdel holes to AMS holes
    * Finished board
    * Removed mode b, changed silkscreen
    * changed name
    * added fuses
    * routed fuses
    * aligned stuff
    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
    [AMS Enerdel Adapter rev7.brd, AMS Enerdel Adapter rev7.sch, AMS Enerdel Adapter rev8.brd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]
2022-06-23 Esf rev 3 (#50)
    * revised schematics to reflect most accurate information
    * added wire gauge key
    [Charging Shutdown Circuit Schematic.sch, Charging Tractive System Schematic.sch]
2022-06-23 Tsal rev6 (#51)
    * new tsal
    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
    [Tractive System Active Light rev6.brd, Tractive System Active Light rev6.csv, Tractive System Active Light rev6.sch]
2022-06-23 Systems diagram (#52)
    * rear diagram
    * more rear diagram
    * shutdown circuit
    * accum work
    * add glvms to psb
    * changes
    * finish front and panel
    * accumulator
    * change radiator wiring
    * Updated accumulator internals
    Need to fix dash connectors, TSAL, TSAL connectors, general symbols update from HyTechTemp
    * update per arvind
    * add hvd
    [External Diagram FSAE 2022.sch]
2022-06-23 ordering files (#53)
    [MainECU rev10.csv]
2022-06-23 Dash rev4 ordering (#54)
    * added order files
    * more order files
    [Tractive System Active Light rev5.csv]
2022-06-23 Power switching board (#55)
    * Replaced mosfets with new device in new library
    * Revert "Replaced mosfets with new device in new library"
    This reverts commit 47685a596586f3a57bfaa4732962c561ce9df098.
    * Created Switching Board rev3 file
    * Replaced MOSFETS with new technology in 2022 library
    * Added fuses on all IO. Realigned entire schematic with grid.
    * Added missing fuse.
    * Added fuse on start button rail. Replaced caps.
    Replaced some caps with ones in library. Changed value of QUAL cap to 680pF. Every cap currently is 0603.
    * Removed RETRY resistors. Replaced EXTVDD cap with one of appropriate voltage rating.
    * Replaced reference resistor dividers with ones in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
    [Power Switching Circuit rev3.brd, Power Switching Circuit rev3.csv, Power Switching Circuit rev3.sch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]
